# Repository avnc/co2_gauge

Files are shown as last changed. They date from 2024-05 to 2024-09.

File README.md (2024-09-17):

# CircuitPython Cute CO2 Gauge

This is a modification of Cyrill Künzi's cute CO2 gauge that he described here: https://kuenzi.dev/co2/. His original implementation integrates with Home Assistant but I needed it to be standalone for my purposes so I used CircuitPython with an Adafruit QT Py ESP32 and an SCD30 CO2 sensor and wrote some [code](code.py).

You'll also need the following libraries in your device's lib directory from the most recent (I used v9.05) CircuitPython bundle:
- `adafruit_bus_device`
- `adafruit_motor`
- `adafruit_register`
- `adafruit_scd30.mpy`

### Build:
- DS3225 Servo, this matches what was used originally so it fits the 3D printed mount (I used this one from [Amazon](https://a.co/d/9nq5n7Z))
- QT Py ESP32-S2 from [Adafruit](https://www.adafruit.com/product/5325). You could use any of the QT Py boards (and numerous others), this just was what I had on-hand. Will likely switch this to a non-WiFi QT Py as a bit of a waste to use this one here.
- A SCD30 CO2 sensor from [Adafruit](https://www.adafruit.com/product/4867) - had one of these left over from a previous project, you could go with one of the cheaper ones like [this](https://www.adafruit.com/product/5190). I'd recommend a true CO2 sensor, not one that only provides eCO2. These seem to be iffy in my experience. If you're comfortable soldering and wiring the I2C connections yourself, you can find a lot of cheap options on AliExpress as well.
- A STEMMA QT cable to easily connect sensor to QT Py ([Adafruit](https://www.adafruit.com/product/4399))
- To connect the motor to the mounting plate you'll need some M4 threaded heat set inserts, 4 M4 bolts (~6mm) and of course a soldering iron with heat set tip to match
- Also obviously helpful: a 3D printer and a color inkjet or other printer. Cyrill's image for the gauge graphic is sized for A4 paper, so careful if you are in US not to allow it to be resized to fit (because then it won't fit correctly in the space).

I also modified the original case to add some venting since I was shoving the ESP32 and the CO2 sensor inside and wanted a little airflow so the readings were reasonable. You can find the modifed part [here](https://github.com/avnc/co2_gauge/tree/main/stl). You'll need Cyrill's original STL also, I've only included the modified part here. It's available in his GitHub [repo](https://github.com/ckuenzi/co2-gauge).

The wiring is very simple. The SCD30 is connected via the STEMMA QT cable to the QT Py's STEMMA QT connector. The motor is connected to the 5v power, ground and TX pins of the QT Py. You'll need to take the data wire out of the 3 pin Dupont female connector the motor comes with and put on a new single pin female connector assuming you have headers on your ESP32. Alternately just solder,

Wiring looks like this:
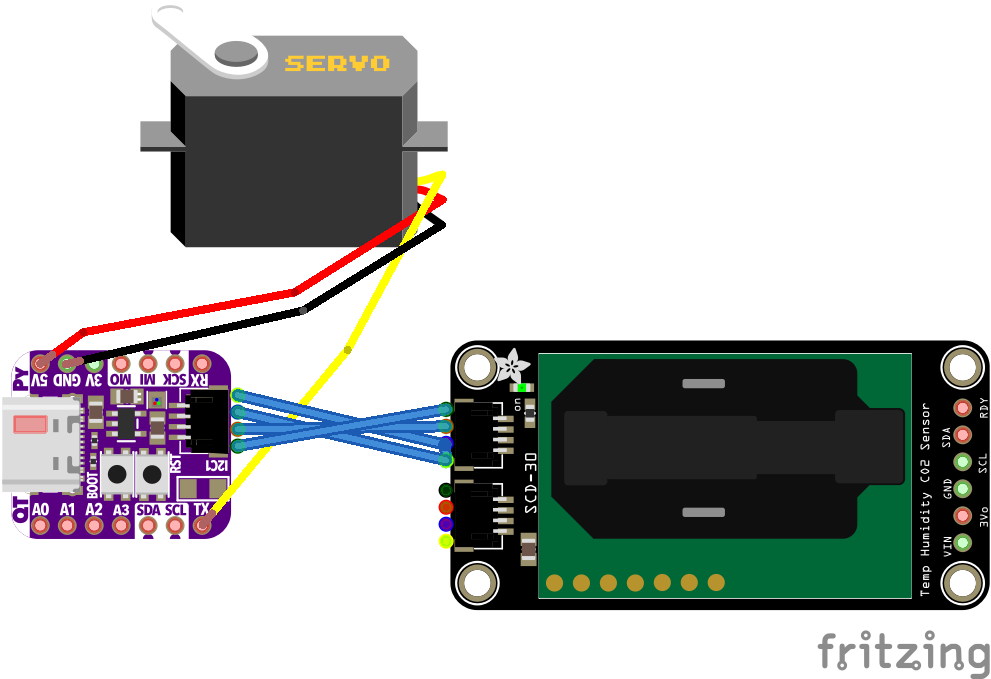
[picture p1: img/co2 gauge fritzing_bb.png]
Fritzing diagram of wiring connections


I printed the modified case part with Amolen wood grain PLA, looks like this when all assembled:
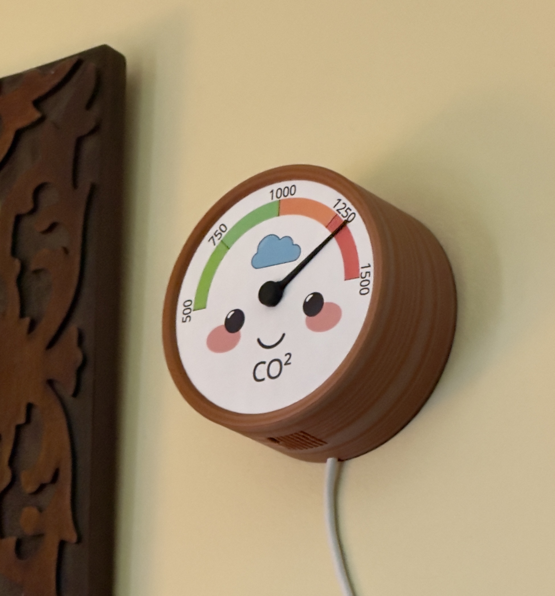
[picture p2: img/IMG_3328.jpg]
Picture of completed gauge printed with wood grain PLA


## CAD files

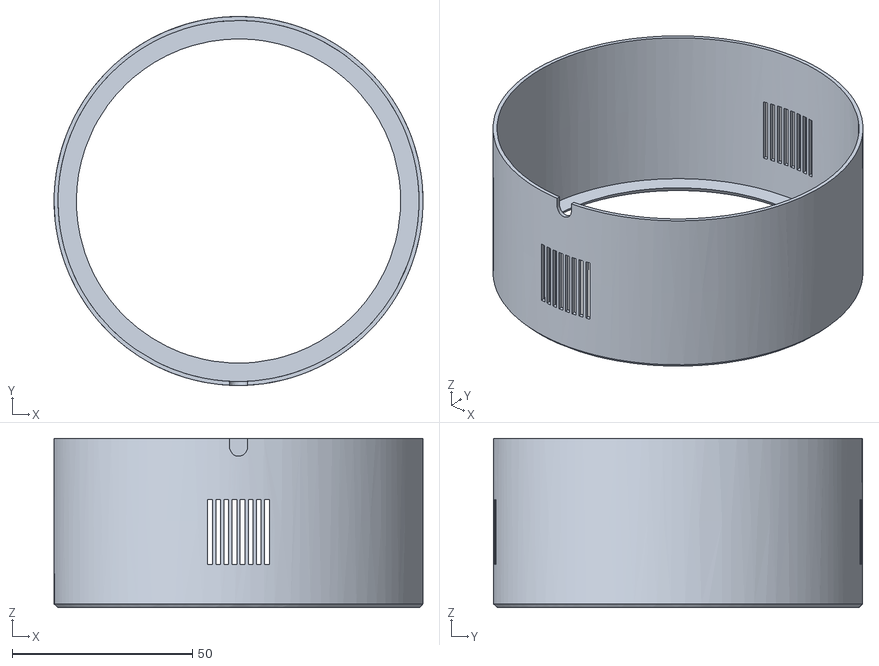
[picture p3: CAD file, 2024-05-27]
stl/Co2 Gauge Housing_vented.stl
102.4 x 102.4 x 47.0

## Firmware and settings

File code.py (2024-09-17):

import board
import time
import pwmio
import adafruit_scd30
from adafruit_motor import servo

i2c = board.STEMMA_I2C()
# i2c = busio.I2C(board.SCL, board.SDA, frequency=50000)
scd = adafruit_scd30.SCD30(i2c)

# note, see info on calibration here: https://learn.adafruit.com/adafruit-scd30/field-calibration
# if self calibration won't work (there are requirements), but you have a known value or can set in fresh air, try forced calibration
# mine needed this calibration, was initially reading high by ~300ppm
scd.self_calibration_enabled = True


# note, we're using a 25kg servo (DS3225), your values may vary
# servo: https://a.co/d/30IFoco
# using an Adafruit QT Py ESP32-S2 board, your pin may vary
servo = servo.Servo(pwmio.PWMOut(board.TX, duty_cycle=0, frequency=50), min_pulse=400, max_pulse=2400)

# adjust these values to match your gauge and servo
SERVO_DIVISOR = 5.55555
ANGLE_MOD = 270

# simple range mapper, like Arduino map() - thanks to todbot  https://github.com/todbot/circuitpython-tricks?tab=readme-ov-file#map-an-input-range-to-an-output-range
def map_range(s, a1, a2, b1, b2):
    return  b1 + ((s - a1) * (b2 - b1) / (a2 - a1))

def setGaugeToValue(servo, co2=500):
    # keep value between 500 and 1500 as this matches the gauge markings
    co2 = min(max(co2, 500), 1500)
    # map the co2 value to an angle between 0 and 180
    angle = map_range(co2, 500, 1500, 180, 0)

    # angle = round(abs((co2 / SERVO_DIVISOR) - ANGLE_MOD))
    print(f"setting to angle {angle}, co2 value is {co2}")
    servo.angle = angle

# test values to see if we're hitting the markings on gauge correctly
def testValuesToMarkings():
    setGaugeToValue(servo, 500)
    time.sleep(3)
    setGaugeToValue(servo, 750)
    time.sleep(3)
    setGaugeToValue(servo, 1000)
    time.sleep(3)
    setGaugeToValue(servo, 1250)
    time.sleep(3)
    setGaugeToValue(servo, 1500)
    time.sleep(3)

while True:
    # this call is not strictly necessary, but it will help if the sleep time is short (< 2secs) and on first read
    if scd.data_available:
        co2 = scd.CO2
        setGaugeToValue(servo, co2)
        print(f"CO2: {co2} PPM")

    # sleep for 30 seconds
    time.sleep(30)

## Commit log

2024-05-27 Added test to check servo position relative to markings on gauge
2024-05-27 Added wiring diagram and modified stl
    [Co2 Gauge Housing_vented.stl]
2024-09-17 Enabled self calibration (and added note with more info)
